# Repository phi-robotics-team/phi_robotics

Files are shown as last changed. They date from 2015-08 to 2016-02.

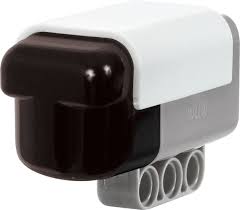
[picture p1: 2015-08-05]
notebook/alpha/2014-15 Phi Alpha Engineering Notebook/index.jpg

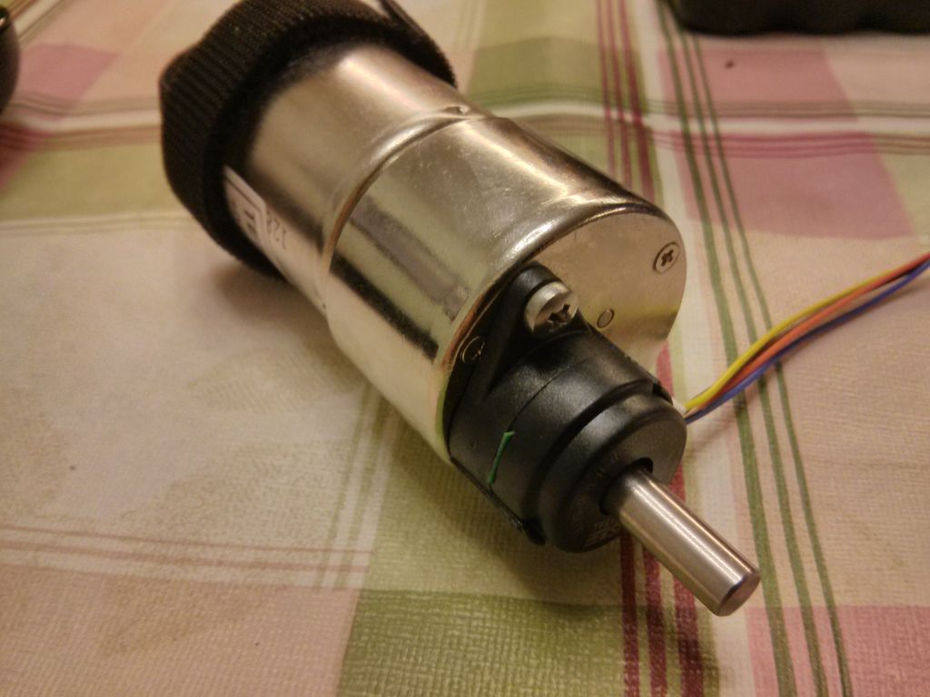
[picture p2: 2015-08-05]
notebook/alpha/2014-15 Phi Alpha Engineering Notebook/F77ZLUBHK46G527.LARGE.jpg

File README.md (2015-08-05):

# PHI Robotics

This repository is for the PHI teams to store all of their files into (replacement for BitSync).
All information should be stored here for easy access by both teams.

## Branch information

### Docs
Contains added once/not changed documents such as PDFs, styleguides, templates, etc

### Pictures
Pictures are in the Google drive area, not in Github

### Code
Contains two sub-directories, one for Alpha and one for Omega

### Notebook
Contains two sub-directories, one for Alpha and one for Omega

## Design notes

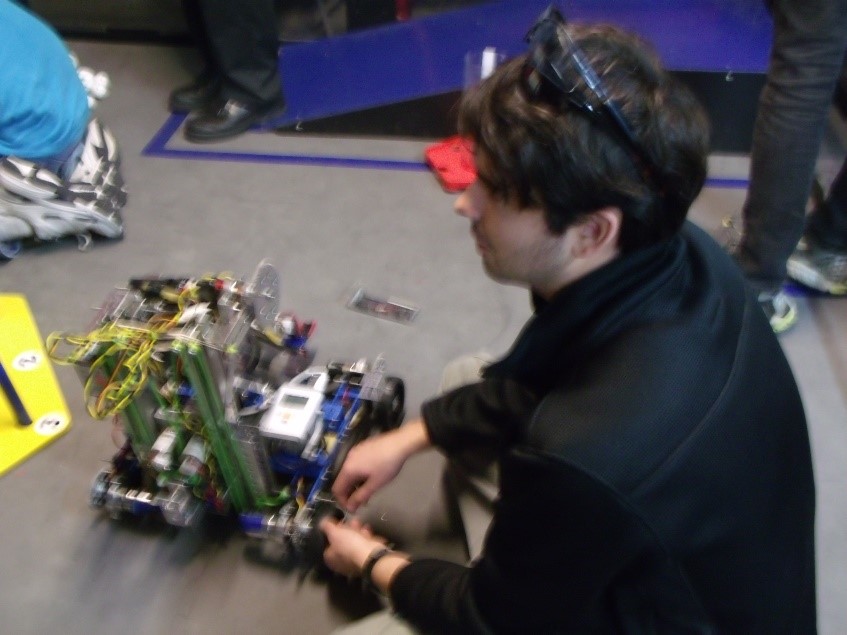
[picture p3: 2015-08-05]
notebook/omega/PHI Notebook 2014-2015/robot 1.jpg

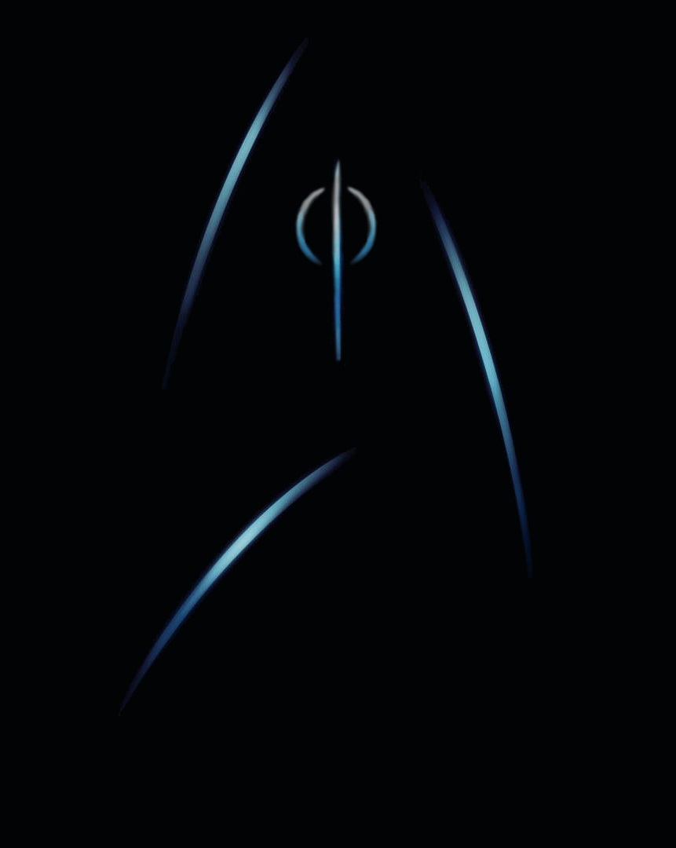
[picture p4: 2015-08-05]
notebook/omega/PHI Notebook 2014-2015/phitrek.jpg

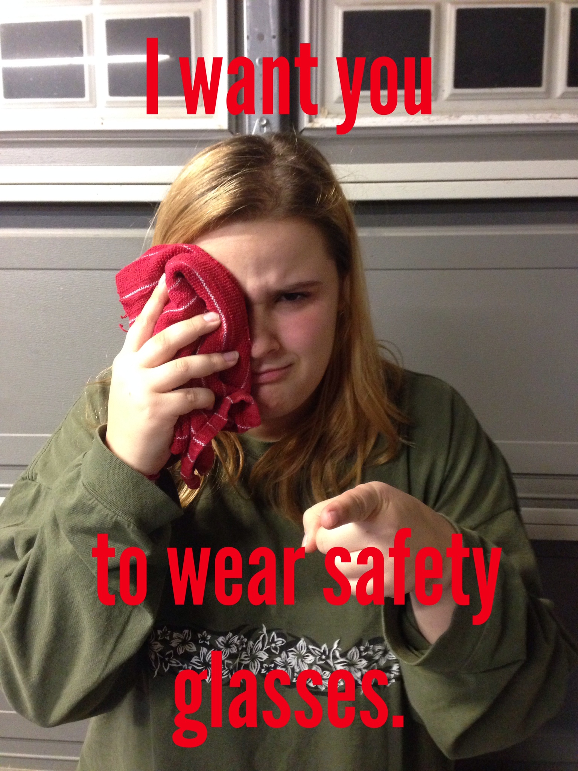
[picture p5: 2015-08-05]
misc/Plankt0n5 2014.11.03_0.JPG

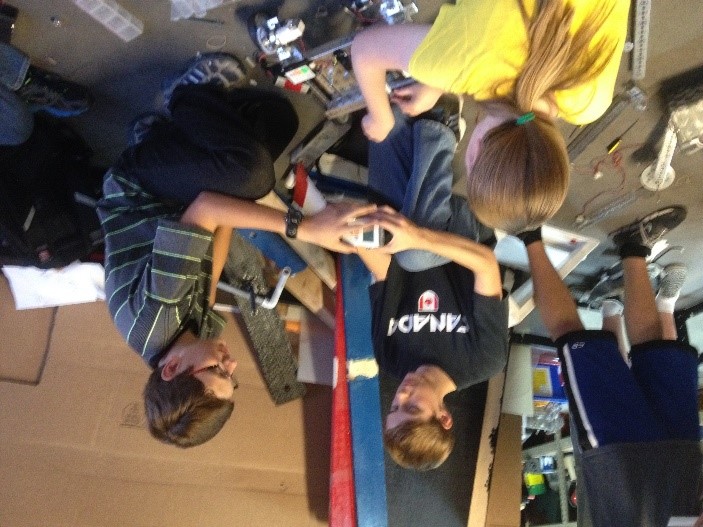
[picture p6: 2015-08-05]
notebook/omega/PHI Notebook 2014-2015/meeting.jpg

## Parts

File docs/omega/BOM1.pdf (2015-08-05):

Part name | Quantity | Game manual rule
PVC Pipe | Two and one-half feet | <RO4a>
Spray paint | Fourteen fluid ounces | <R12>
Lexan plastic | Three square feet | <RO4a>
Craft foam | Nine square inches | <RO4a>
Zip ties | Fifty zip ties | <RO5>
Surgical rubber tubing | Four feet | <RG10>
1/16 inch metal wire | Seven feet | <R10d>
Wire sheathing | Seven inches | <R10d>
Duct tape | Forty inches | <RO5>
Sheet metal | Twenty-one square inches | <RO4a>
Light Bars | Two | <R12>
Liquid accent highlighet ink | A 1/16 pen's worth | <R12>
Stickers | Thirteen | <R12>
Vectran | One-hundred inches | <RO4a>
Light Strip | One | <R12>
Carbon Fiber | Three square feet | <R12>
Printer Paper | Eight square inches | <R12>
Extended Power Wires | Three feet | <R10d>
Safety wire | Nine inches | <RO5>
Bungie | Six inches | <RG10>
Heat shrink | Seven inches | <R10d>
Threadlock | Two drops | <RO5>
Elmer's glue | Two fluid ounces | <R12>
Heavy duty silicone lube | One-quarter fluid ounce | <RO6>
Non-slip drawer liner | One-hundred square inches | <RO4a>
Phone cables | Seventy-five inches | <R10d>
ABS plastic | Thirty-two square inches | <RO4a>
Rivets | Twenty-one | <R12>
.40 cal shell casings | Seven | <RO4b>
Washers | Twenty-seven | <RO5>
Fender washers | One | <RO5>
Screen door roller | One | <RO4c>
Solder | Two inches | <RO5>
WD40 | One-sixteenth fluid once | <RO6>
Super glue | Three ounces | <RO5>
24 guage wire | Twelve inches | <R10d>
Velcro | Three inches | <RO5>
Nine-volt battery | One | <R11di>
Thread | Four feet | <RO4b>
Prototype board | One | <R11d>
Resister | Three | <RO8d>
GY-80 | One | <RO8d>
Light sensor | One | <RO8d>
Bowled over led strip | One | <R11e>
Surge protector usb | One | <RO8c>
Power polles | Four | <R10c>
Anderson connectors | Two | <R10c>
Axicom D2N relay | One | <RO8d>
Arduino NANO | One | <R11dii>
Solder board | One | <RO8Dd>
MUX | One | <R11b>
Ferrite choke | Two | <RO8c>
Poliester netting | One foot square | <RO4b>
Drawer slides | Three | <RO4c>
BILL OF MATERIALS | 4322

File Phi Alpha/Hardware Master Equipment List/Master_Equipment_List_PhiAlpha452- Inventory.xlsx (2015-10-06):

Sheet: Inventory List
INVENTORY LIST |  |  |  |  |  |  |  |  | Inventory
 | part Number | Part Name | Description | size | Color | Vendor | Price | units/pack | Quantity | Total
Channels
 | AZ39069 | TETRIX_739069_2012 | 416mm Channel |  |  | Pitsco(tetrix) | $17.95 | 1 | 0 | $0.00
 | AZ39068 | TETRIX_739068_2012 | 288mm Channel |  |  | Pitsco(tetrix) | $27.95 | 2 | 0 | $0.00
 | AZ39067 | TETRIX_739067_2012 | 160m Channel |  |  | Pitsco(tetrix) | $16.95 | 2 | 0 | $0.00
 | AZ39066 | TETRIX_739066_2012 | 96mm Channel |  |  | Pitsco(tetrix) | $11.95 | 2 | 0 | $0.00
 | AZ39065 | TETRIX_739065_2012 | 32mm Channel |  |  | Pitsco(tetrix) | $9.95 | 2 | 0 | $0.00
 |  |  |  |  |  |  |  |  | 0
Brackets |  |  |  |  |  |  |  |  | 0
 | AZ39061 | TETRIX_739061_2012 | Flat Bracket |  |  | Pitsco(tetrix) | $5.95 | 2 | 0 | $0.00
 | AZ39062 | TETRIX_739062_2012 | L Bracket |  |  | Pitsco(tetrix) | $4.95 | 2 | 0 | $0.00
 | AZ39281 |  | Inside Corner Bracket |  |  | Pitsco(Tetrix) | $4.95 | 2 | 0 | $0.00
 | AZ39270 | TETRIX_739270_2013 | Inside C Connector |  |  | Pitsco(tetrix) | $4.95 | 2 | 0 | $0.00
 |  |  |  |  |  |  |  |  | 0
Angles |  |  |  |  |  |  |  |  | 0
 | AZ39071 | TETRIX_739071_2012 | 288mm Angle |  |  | Pitsco(tetrix) | $13.95 | 2 | 0 | $0.00
 | AZ39072 | TETRIX_739072_2012 | 144mm Angle |  |  | Pitsco(tetrix) | $10.95 | 2 | 0 | $0.00
 |  |  |  |  |  |  |  |  | 0
Plates |  |  |  |  |  |  |  |  | 0
 | AZ39073 | TETRIX_739073_2012 | Flat Building Plate |  |  | Pitsco(tetrix) | $12.95 | 2 | 0 | $0.00
 |  |  |  |  |  |  |  |  | 0
Axles/Shafts |  |  |  |  |  |  |  |  | 0
 | AZ39088 |  | Axle | 100mm |  | Pitsco(tetrix) | $15.95 | 6 | 0 | $0.00
 | AZ35871 |  | Axle | 250mm |  | Pitsco(tetrix) | $15.95 | 3 | 0 | $0.00
 | AZ39172 |  | Axle Hub | Axle |  | Pitsco(tetrix) | $6.95 | 2 | 0 | $0.00
 | W39172 | TETRIX_739172_ 2012 | Axel Hub |  |  | Pitsco(tetrix) | $6.95 | 2 | 0 | $0.00
 | AZ39092 | TETRIX_739092_ 2012 | Axel Collar |  |  | Pitsco(tetrix) | $3.95 | 6 | 0 | $0.00
 | W39100 | TETRIX_739100_2012 | 1/8" Axel Spacer |  |  | Pitsco(tetrix) | $1.95 | 12 | 0 | $0.00
 | W39101 | TETRIX_739101_2012 | 3/8" Axel Spacer |  |  | Pitsco(tetrix) | $0.95 | 6 | 0 | $0.00
 |  |  |  |  |  |  |  |  | 0
Chains/Sprockets |  |  |  |  |  |  |  |  | 0
 | AZ39173 |  | Chain with Links |  |  | Pitsco(tetrix) | $13.95 | 5 feet | 0 | $0.00
 | AZ39171 | Tetrix Max 32-Tooth Sprocket Pack | Chain sprockets | 32 |  | Pitsco(tetrix) | $29.95 | 2 | 0 | $0.00
 | Az39169 | Tetrix Max 24-Tooth Sprocket Pack | Chain sprockets | 24 |  | Pitsco(tetrix) | $22.95 | 2 | 0 | $0.00
 | Az39165 | Tetrix Max 16-Tooth Sprocket Pack | Chain sprockets | 16 |  | Pitsco(tetrix) | $16.95 | 2 | 0 | $0.00
 |  |  |  |  |  |  |  |  | 0
Gears |  |  |  |  |  |  |  |  | 0
 | AZ39085 | TETRIX_731901_120_2013 | 120-Tooth Gear |  |  | Pitsco(tetrix) | $27.95 | 2 | 0 | $0.00
 | AZ39086 | TETRIX_739086_2012 | 80-Tooth Gear |  |  | Pitsco(tetrix) | $17.95 | 1 | 0 | $0.00
 | AZ39028 | TETRIX_739028_2012 | 40-Tooth Gear |  |  | Pitsco(tetrix) | $22.95 | 2 | 0 | $0.00
 | AZ39090 | TETRIX_739090_2012 | Gear Hub Spacer |  |  | Pitsco(tetrix) | $6.95 | 2 | 0 | $0.00
 | AZ38007 | Tetrix Max Vevel Gear & Acetal Bearings |  |  |  | Pitsco(tetrix) | $29.95 | 1 | 0 | $0.00
 | AZ39375 | Tetrix Max Worm Gear Box | 4:1 worm gear |  |  | Pitsco(tetrix) | $34.95 | 1 | 0 | $0.00
 |  |  |  |  |  |  |  |  | 0
Motors |  |  |  |  |  |  |  |  | 0
 | AM-3103 | NEVEREST_60_MOTOR | Motor with encoder | 1.46"dia |  | Andymark | $25.00 | 1 | 0 | $0.00
 | AZ39530 | TETRIX_739083_2012 | TETRIX DC Motor |  |  | Pitsco(tetrix) | $24.95 | 1 | 0 | $0.00 | 6 DC motors | Order from andy aMark with encoder.
 | AZ39079 | TETRIX_739079_2012 | Motor Hub |  |  | Pitsco(tetrix) | $5.95 | 2 | 0 | $0.00
 | AZ39089 |  | Motor Mount |  |  | Pitsco(tetrix) | $15.95 | 1 | 0 | $0.00
 | AZ39376 | TETRIX_739089_2012 | DC Motor Mount |  |  | Pitsco(tetrix) | $15.95 | 1 | 0 | $0.00 |  | Verify
 | W3989 | TETRIX_MAXMOTORMOUNT | MOTOR MOUNT |  |  | Pitsco(tetrix) | $15.95 | 1 | 0 | $0.00
 |  | TETRIX_739172_ 2012 | Motor Mount Screw |  |  | Pitsco(tetrix) |  |  | 0 | $0.00
 | AZ31903 |  | Motor power cable |  |  | Pitsco(tetrix) | $1.95 | 1 | 0 | $0.00
 | AZ36465 | TETRIX_731903_2012 | Motor Power Wire |  |  | Pitsco(tetrix) | $1.95 | 1 | 0 | $0.00
 | AM-2992 | hall_affect_encoder_cable | encoder cable with 4_pin connector | 19.5" |  | AndyMark | $5.00 | 1 | 0 | $0.00
 | w380000 | TETRIX_738000_2012 | Motor Encoder |  |  | Pitsco(tetrix) | $79.95 | 1 | 0 | $0.00
 |  |  |  |  |  |  |  |  | 0
Servo's |  |  |  |  |  |  |  |  | 0
 | AZ39197 |  | 180 servo |  |  | Pitsco(tetrix) | $24.95 | 1 | 0 | $0.00
 | AZ39060 | TETRIX_739060_2012 | Single Standard Scale Servo Bracket |  |  | Pitsco(tetrix) | $9.95 | 2 | 0 | $0.00
 | AZ39197 | TETRIX_739172_ 2012 | Standard-Scale HS-485HB Servo Motor |  |  | Pitsco(tetrix) | $24.95 | 1 | 0 | $0.00
 |  |  |  |  |  |  |  |  | 0
Controllers / Power distribution |  |  |  |  |  |  |  |  | 0
 | AZ34303 | Core_motor Controller |  |  |  | Pitsco(tetrix) | $89.95 | 1 | 0 | $0.00 |  | have 3- don't know how many work.
 |  | Core_Power_Distribution_Module |  |  |  |  |  |  | 0 | $0.00 |  | Have 1 new one
 | AZ34302 | Core_Servo_Controller |  |  |  | Pitsco(tetrix) | $79.95 | 1 | 0 | $0.00
 |  |  |  |  |  |  |  |  | 0
Wires |  |  |  |  |  |  |  |  | 0
 |  | Power (14 gauge (black white)
 | 7088k211 | Retracting Cable (300V AC-Light Duty) | 18 Gauge 2 wire | 2ft, 18ga |  | (McMaster-Carr) | $25.52 | 1 | 0 | $0.00
 |  |  |  |  |  |  |  |  | 0
Wheels |  |  |  |  |  |  |  |  | 0
 | AZ39055 | TETRIX_739055_2012 | 4" Wheel | 4" |  | Pitsco(tetrix) | $19.95 | 1 | 0 |  |  | Check with Andy Mark
 | AZ36466 | TETRIX_736466_2012 | TETRIX MAX Omni Wheel Pack | 4 inch |  | Pitsco(tetrix) | $29.95 | 2 | 0 | $0.00
 | W36466 |  | TETRIX MAX Omni Wheel Pack | 4" |  | Pitsco(tetrix) | $29.95 | 2 | 0 | $0.00
 |  |  |  |  |  |  |  |  | 0
Screws/Nuts |  |  |  |  |  |  |  |  | 0
 | AZ39098 |  | Small screw | Small |  | pitsco(Tetrix) | $9.95 | 100 | 0 | $0.00
 | AZ39097 |  | Medium screw | Medium |  | Pitsco(tetrix) | $9.95 | 100 | 0 | $0.00
 | AZ39111 |  | Flat screws | 3 8 |  | Pitsco(tetrix) | $8.95 | 50 | 0 | $0.00
 | AZ39094 | TETRIX_739094_2013 | Kep Nut |  |  | Pitsco(tetrix) | $2.95 | 100 | 0 | $0.00
 | W39097 | TETRIX_739097_2013 | 1/2" Socket Head Cap Screw |  |  | Pitsco(tetrix) | $9.95 | 100 | 0 | $0.00
 | W39098 | TETRIX_739098_2012 | 5/16" Socket Head Cap Screw |  |  | Pitsco(tetrix) | $9.95 | 100 | 0 | $0.00
 | W39111 | TETRIX_739111_2012 | Button Head Cap Screw |  |  | Pitsco(tetrix) | $8.95 | 50 | 0 | $0.00
 |  |  |  |  |  |  |  |  | 0
 |  |  |  |  |  |  |  |  | 0
Batteries |  |  |  |  |  |  |  |  | 0
 | AZ39057 | TETRIX_739057_2012 | Battery Pack | 12 Volt - NIMH |  | Pitsco(tetrix) | $49.95 | 1 | 0 | $0.00
 | AZ38009 | TETRIX_738009_BATPACK_BRKT_2013 | Battery Clip |  |  | Pitsco(tetrix) | $5.95 | 1 | 0 | $0.00
 | az39830 | TETRIX | Battery Pack Charger |  |  | Pitsco(tetrix) | $24.95 | 1 | 0 | $0.00
 |  |  |  |  |  |  |  |  | 0
Tools |  |  |  |  |  |  |  |  | 0
 | AZ39217 |  | Chain Breaker Tool |  |  | Pitsco(tetrix) | $16.95 |  | 0 | $0.00
 | W39104 |  | Hex Keys | 7/64, 3/32, 1/16, 5/64 |  | Pitsco(tetrix) | $0.95 | 4 each size | 0 | $0.00
 |  |  |  |  |  |  |  |  | 0
Miscellaneous Small Parts |  |  |  |  |  |  |  |  | 0
 | 8800k43 |  | Kevlar Thread | 346 |  | McMaster carr | $27.17 | 66 yards | 0 | $0.00
 | 87635k63 |  | polyester thread | 693 |  | McMaster carr | $12.77 | 120 yards | 0 | $0.00
 | 3434T33 |  | thread pulleys | 3 64 |  | MCMaster carr | $1.52 | 1 | 0 | $0.00
 |  |  |  |  |  |  |  |  | 0
 |  |  |  |  |  |  |  |  | 0
 | W39102 | TETRIX_739102_2012 | 1" Stand-off |  |  | Pitsco(tetrix) | $3.95 | 12 | 0 | $0.00
 | W39107 | TETRIX_739107_2013 | 32mm Stand-of |  |  | Pitsco(tetrix) | $4.95 | 12 | 0 | $0.00
 | AZ39091 | TETRIX_739091_2013 | Bronze Bushing |  |  | Pitsco(tetrix) | $13.95 | 12 | 0 | $0.00
 | W39120 | TETRIX_739120_2012 | Hard Point Connector |  |  | Pitsco(tetrix) | $12.00 | 12 | 0 | $0.00
 |  |  |  |  |  |  |  |  |  | $0.00

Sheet: order (4)
 | part Number | Part Name | Description | size | Color | Vendor | Price | units/pack | Quantity | Total
 | 7088k211 | Retracting Cable (300V AC-Light Duty) | 18 Gauge 2 wire | 2ft, 18ga |  | McMaster-Carr | $25.52 | 1 | 1 | $25.52
 | AM-2992 | hall_affect_encoder_cable | encoder cable with 4_pin connector | 19.5" |  | Andy Mark | $5.00 | 1 | 8 | $40.00
 | AM-2964 | Nev Rest 40 Motor | 40:1 Motor |  |  | Andy Mark | $25.00 | 1 | 4 | $100.00
 | am-3211 | Bonded Wire | 18 Gauge 2 wire 20'' | 20'', 18 |  | Andy Mark | $7.00 | 25 | 1 | $7.00
 | AM-0980 | Polycarbonate sheet | 24"x24", 0.118" | 0.118" |  | Andy Mark | $20.00 | 1 | 2 | $40.00
 |  | Gyro |  |  |  | HiTechnic
 | 9697T2 | Easy-ID Low-Voltage Cable | 18 Gauge 2 wire black/red | 50ft, 18 ga |  | McMaster carr | $15.50 | 1 | 0 | $0.00 |  | McCloud may be getting wire
 | 73095K48 | Heat-Shrink Tubing Assortments |  |  |  | McMaster carr | $27.12 | 1 | 0 | $0.00
 | 45-2018 | Color Sensor |  |  |  | Modern Robotics, Inc | $36.95 | 1 | 0 | $0.00 |  | Order if we can program the Hi technic sensor.
 | AZ39062 | TETRIX_739062_2012 | L Bracket |  |  | Pitsco(tetrix) | $4.95 | 2 | 0 | $0.00
 | AUA3030 | Core Device Interface Module |  |  |  | Modern Robotics, Inc. | $67.95 | 1 | 0 | $0.00 |  | Order if we go with the color sensor.
 | GPF0310 | Logitec F310 Gamepad |  |  |  | Modern Robotics, Inc. | $24.95 | 1 | 1 | $24.95
 | W36468 | Tetrix Max Tank Tread Kit |  |  |  | Pitsco (Tetrix) | $99.95 | 1 | 1 | $99.95
 | W36464 | Tetrix Max Tank Tread Inserts |  |  |  | Pitsco (Tetrix) | $17.95 | 1 | 1 | $17.95
 | W39069/AZ39069 | TETRIX_739069_2012 | 416mm Channel | 16.4 |  | Pitsco(tetrix) | $17.95 | 1 | 0 | $0.00
 | W39068/AZ39068 | TETRIX_739068_2012 | 288mm Channel | 11.3 |  | Pitsco(tetrix) | $27.95 | 2 | 1 | $27.95
 | W39067/AZ39067 | TETRIX_739067_2012 | 160m Channel | 6.3 |  | Pitsco(tetrix) | $16.95 | 2 | 1 | $16.95
 | W39066/AZ39066 | TETRIX_739066_2012 | 96mm Channel | 3.8 |  | Pitsco(tetrix) | $11.95 | 2 | 3 | $35.85
 | W39065/AZ39065 | TETRIX_739065_2012 | 32mm Channel | 1.3 |  | Pitsco(tetrix) | $9.95 | 2 | 2 | $19.90
 | W39061/AZ39061 | TETRIX_739061_2012 | Flat Bracket |  |  | Pitsco(tetrix) | $5.95 | 2 | 4 | $23.80
 | W39281/AZ39281 |  | Inside Corner Bracket |  |  | Pitsco(Tetrix) | $4.95 | 2 | 3 | $14.85
 | W39270/AZ39270 | TETRIX_739270_2013 | Inside C Connector |  |  | Pitsco(tetrix) | $4.95 | 2 | 4 | $19.80
 | W39071/AZ39071 | TETRIX_739071_2012 | 288mm Angle |  |  | Pitsco(tetrix) | $13.95 | 2 | 2 | $27.90
 | AZ39172 |  | Axle Hub | Axle |  | Pitsco(tetrix) | $6.95 | 2 | 0 | $0.00
 | W39072/AZ39072 | TETRIX_739072_2012 | 144mm Angle |  |  | Pitsco(tetrix) | $10.95 | 2 | 2 | $21.90
 | W39073/AZ39073 | TETRIX_739073_2012 | Flat Building Plate |  |  | Pitsco(tetrix) | $12.95 | 2 | 1 | $12.95
 | W39100 | TETRIX_739100_2012 | 1/8" Axel Spacer |  |  | Pitsco(tetrix) | $1.95 | 12 | 0 | $0.00
 | W39101 | TETRIX_739101_2012 | 3/8" Axel Spacer |  |  | Pitsco(tetrix) | $0.95 | 6 | 0 | $0.00
 | W39088/AZ39088 |  | Axle | 100mm |  | Pitsco(tetrix) | $15.95 | 6 | 1 | $15.95
 | W35871/AZ35871 |  | Axle | 250mm |  | Pitsco(tetrix) | $15.95 | 3 | 1 | $15.95
 | W39173/AZ39173 |  | Chain with Links |  |  | Pitsco(tetrix) | $13.95 | 5 feet | 0 | $0.00
 | W39171/AZ39171 | Tetrix Max 32-Tooth Sprocket Pack | Chain sprockets | 32.0 |  | Pitsco(tetrix) | $29.95 | 2 | 0 | $0.00
 | W39169/Az39169 | Tetrix Max 24-Tooth Sprocket Pack | Chain sprockets | 24.0 |  | Pitsco(tetrix) | $22.95 | 2 | 0 | $0.00
 | W39165/Az39165 | Tetrix Max 16-Tooth Sprocket Pack | Chain sprockets | 16.0 |  | Pitsco(tetrix) | $16.95 | 2 | 0 | $0.00
 | W39172 | TETRIX_739172_ 2012 | Axel Hub |  |  | Pitsco(tetrix) | $6.95 | 2 | 4 | $27.80
 | W39092/AZ39092 | TETRIX_739092_ 2012 | Axel Collar |  |  | Pitsco(tetrix) | $3.95 | 6 | 2 | $7.90
 | W39085/AZ39085 | TETRIX_731901_120_2013 | 120-Tooth Gear |  |  | Pitsco(tetrix) | $27.95 | 2 | 1 | $27.95
 | AZ39086 | TETRIX_739086_2012 | 80-Tooth Gear |  |  | Pitsco(tetrix) | $17.95 | 1 | 0 | $0.00
 | AZ39028 | TETRIX_739028_2012 | 40-Tooth Gear |  |  | Pitsco(tetrix) | $22.95 | 2 | 0 | $0.00
 | W39090/AZ39090 | TETRIX_739090_2012 | Gear Hub Spacer |  |  | Pitsco(tetrix) | $6.95 | 2 | 4 | $27.80
 | AZ38007 | Tetrix Max Vevel Gear & Acetal Bearings |  |  |  | Pitsco(tetrix) | $29.95 | 1 | 0 | $0.00
 | AZ39375 | Tetrix Max Worm Gear Box | 4:1 worm gear |  |  | Pitsco(tetrix) | $34.95 | 1 | 0 | $0.00
 | AZ39060 | TETRIX_739060_2012 | Single Standard Scale Servo Bracket |  |  | Pitsco(tetrix) | $9.95 | 2 | 1 | $9.95
 | AZ34303 | Core_motor Controller |  |  |  | Pitsco(tetrix) | $89.95 | 1 | 0 | $0.00 |  | have 3- don't know how many work.
 | AM-3103 | NEVEREST_60_MOTOR | Motor with encoder | 1.46"dia |  | Andymark | $25.00 | 1 | 0 | $0.00
 | AZ39530 | TETRIX_739083_2012 | TETRIX DC Motor |  |  | Pitsco(tetrix) | $24.95 | 1 | 0 | $0.00 | 6 DC motors | Order from andy aMark with encoder.
 | AZ39079 | TETRIX_739079_2012 | Motor Hub |  |  | Pitsco(tetrix) | $5.95 | 2 | 0 | $0.00
 | AZ39089 |  | Motor Mount |  |  | Pitsco(tetrix) | $15.95 | 1 | 0 | $0.00
 | AZ39376 | TETRIX_739089_2012 | DC Motor Mount |  |  | Pitsco(tetrix) | $15.95 | 1 | 0 | $0.00 |  | Verify
 | W3989 | TETRIX_MAXMOTORMOUNT | MOTOR MOUNT |  |  | Pitsco(tetrix) | $15.95 | 1 | 0 | $0.00
 |  | TETRIX_739172_ 2012 | Motor Mount Screw |  |  | Pitsco(tetrix) |  |  | 0 | $0.00
 | W31903/AZ31903 |  | Motor power cable |  |  | Pitsco(tetrix) | $1.95 | 1 | 0 | $0.00
 | AZ36465 | TETRIX_731903_2012 | Motor Power Wire |  |  | Pitsco(tetrix) | $1.95 | 1 | 0 | $0.00
 | AZ34302 | Core_Servo_Controller |  |  |  | Pitsco(tetrix) | $79.95 | 1 | 0 | $0.00
 | w380000 | TETRIX_738000_2012 | Motor Encoder |  |  | Pitsco(tetrix) | $79.95 | 1 | 0 | $0.00
 | W39104 |  | Hex Keys | 7/64, 3/32, 1/16, 5/64 |  | Pitsco(tetrix) | $0.95 | 4 each size | 2 | $1.90
 | W39102 | TETRIX_739102_2012 | 1" Stand-off |  |  | Pitsco(tetrix) | $3.95 | 12 | 1 | $3.95
 | AZ39197 |  | 180 servo |  |  | Pitsco(tetrix) | $24.95 | 1 | 0 | $0.00
 | W39107 | TETRIX_739107_2013 | 32mm Stand-of |  |  | Pitsco(tetrix) | $4.95 | 12 | 1 | $4.95
 | AZ39197 | TETRIX_739172_ 2012 | Standard-Scale HS-485HB Servo Motor |  |  | Pitsco(tetrix) | $24.95 | 1 | 0 | $0.00
Channels
Brackets
Angles
Plates
Axles/Shafts
Chains/Sprockets
Gears
 |  | Power (14 gauge (black white)
Motors
Servo's
Controllers / Power distribution
 | W39055/AZ39055 | TETRIX_739055_2012 | 4" Wheel | 4" |  | Pitsco(tetrix) | $19.95 | 1 | 0 | $0.00 |  | Check with Andy Mark
 | AZ36466 | TETRIX_736466_2012 | TETRIX MAX Omni Wheel Pack | 4 inch |  | Pitsco(tetrix) | $29.95 | 2 | 0 | $0.00
 | W36466 |  | TETRIX MAX Omni Wheel Pack | 4" |  | Pitsco(tetrix) | $29.95 | 2 | 0 | $0.00
 |  | Core_Power_Distribution_Module |  |  |  |  |  |  | 0 | $0.00 |  | Have 1 new one
Sensors
Wires
Wheels
Tread Kits
 | 94985K911 | Super Adhesive-back General Purpose Hook and Loop | 2" x 5 ft |  |  | McMaster-Carr | $17.91 | 1 | 0 | $0.00
Polycarbonate Sheet
 | AZ39098 |  | Small screw | Small |  | pitsco(Tetrix) | $9.95 | 100 | 0 | $0.00
 | AZ39097 |  | Medium screw | Medium |  | Pitsco(tetrix) | $9.95 | 100 | 0 | $0.00
 | AZ39111 |  | Flat screws | 3 8 |  | Pitsco(tetrix) | $8.95 | 50 | 0 | $0.00
 | AZ39094 | TETRIX_739094_2013 | Kep Nut |  |  | Pitsco(tetrix) | $2.95 | 100 | 0 | $0.00
 | W39097 | TETRIX_739097_2013 | 1/2" Socket Head Cap Screw |  |  | Pitsco(tetrix) | $9.95 | 100 | 0 | $0.00
 | W39098 | TETRIX_739098_2012 | 5/16" Socket Head Cap Screw |  |  | Pitsco(tetrix) | $9.95 | 100 | 0 | $0.00
 | W39111 | TETRIX_739111_2012 | Button Head Cap Screw |  |  | Pitsco(tetrix) | $8.95 | 50 | 0 | $0.00
Velcro
Screws/Nuts
 | AZ39057 | TETRIX_739057_2012 | Battery Pack | 12 Volt - NIMH |  | Pitsco(tetrix) | $49.95 | 1 | 0 | $0.00
 | AZ38009 | TETRIX_738009_BATPACK_BRKT_2013 | Battery Clip |  |  | Pitsco(tetrix) | $5.95 | 1 | 0 | $0.00
 | az39830 | TETRIX | Battery Pack Charger |  |  | Pitsco(tetrix) | $24.95 | 1 | 0 | $0.00
 | AZ39217 |  | Chain Breaker Tool |  |  | Pitsco(tetrix) | $16.95 |  | 0 | $0.00
Batteries
Tools
 | 8800k43 |  | Kevlar Thread | 346.0 |  | McMaster carr | $27.17 | 66 yards | 0 | $0.00
 | 87635k63 |  | polyester thread | 693.0 |  | McMaster carr | $12.77 | 120 yards | 0 | $0.00
 | 3434T33 |  | thread pulleys | 3 64 |  | MCMaster carr | $1.52 | 1 | 0 | $0.00
Miscellaneous Small Parts
 | AZ39091 | TETRIX_739091_2013 | Bronze Bushing |  |  | Pitsco(tetrix) | $13.95 | 12 | 0 | $0.00
 | W39120 | TETRIX_739120_2012 | Hard Point Connector |  |  | Pitsco(tetrix) | $12.00 | 12 | 0 | $0.00
 |  |  |  |  |  |  |  |  |  | $721.32
 |  | Tread & Inserts
 |  | Color Sensor
 |  | 18 gauge wire
 |  | Polycarbonate
 |  | Color Sensor | Check with Caddics
 |  | Velcro

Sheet: Sheet1
part Number | Part Name | Description | size | Color | Vendor | Price | units/pack | Quantity | Total
AZ39069 |  | C-channel | 416mm |  | Pitsco(Tetrix) | $17.95 | 1 | 4 | $71.80 | 16.64 | 416 | 16.64
AZ39281 |  | Inside Corner Bracket |  |  | Pitsco(Tetrix) | $4.95 | 2 | 4 | $19.80 |  | 288 | 11.52
AZ39098 |  | Small screw | Small |  | pitsco(Tetrix) | $9.95 | 100 | 1 | $9.95
AZ39097 |  | Medium screw | Medium |  | Pitsco(tetrix) | $9.95 | 100 | 1 | $9.95
AZ39094 |  | Kep Nuts |  |  | Pitsco(tetrix) | $2.95 | 100 | 2 | $5.90
AZ39111 |  | Flat screws | 3 8 |  | Pitsco(tetrix) | $8.95 | 50 | 1 | $8.95
AZ39197 |  | 180 servo |  |  | Pitsco(tetrix) | $24.95 | 1 | 4 | $99.80
AZ39172 |  | Axle Hub | Axle |  | Pitsco(tetrix) | $6.95 | 2 | 4 | $27.80
AZ39088 |  | Axle | 100mm |  | Pitsco(tetrix) | $15.95 | 6 | 1 | $15.95
AZ35871 |  | Axle | 250mm |  | Pitsco(tetrix) | $15.95 | 3 | 2 | $31.90
AZ39079 |  | Motor Shaft Hubs | Motor |  | Pitsco(tetrix) | $5.95 | 2 | 2 | $11.90
AZ39173 |  | Chain with Links |  |  | Pitsco(tetrix) | $13.95 | 5 feet | 1 | $13.95
AZ39057 |  | 12volt nimh battery pack | 12 volt |  | Pitsco(tetrix) | $49.95 | 1 | 2 | $99.90
AZ39104 |  | Hex Keys | Each size |  | Pitsco(tetrix) | $0.95 | 4 each size | 15 | $14.25
AZ39217 |  | Chain Breaker Tool |  |  | Pitsco(tetrix) | $16.95 | 1 | 1 | $16.95
 |  | motor controller |  |  | Pitsco(tetrix) |  |  |  | $0.00
 |  | servo controller |  |  | Pitsco(tetrix) |  |  |  | $0.00
AZ39055 |  | Wheel | 4” |  | Pitsco(tetrix) | $19.95 | 1 | 4 | $79.80
AZ39089 |  | Motor Mount |  |  | Pitsco(tetrix) | $15.95 | 1 | 6 | $95.70
AZ31903 |  | Motor power cable |  |  | Pitsco(tetrix) | $1.95 | 1 | 5 | $9.75
8800k43 |  | Kevlar Thread | 346 |  | McMaster carr | $27.17 | 66 yards | 1 | $27.17
87635k63 |  | polyester thread | 693 |  | McMaster carr | $12.77 | 120 yards | 1 | $12.77
3434T33 |  | tread pulleys | 3 64 |  | MCMaster carr | $1.52 | 1 | 4 | $6.08
AZ34303 | Core_motor Controller |  |  |  | Pitsco(tetrix) | $89.95 | 1
 | Core_Power_Distribution_Module
AZ34302 | Core_Servo_Controller |  |  |  | Pitsco(tetrix) | $79.95 | 1
AZ39085 | TETRIX_731901_120_2013 | 120-Tooth Gear |  |  | Pitsco(tetrix) | $27.95 | 2
AZ36465 | TETRIX_731903_2012 | Motor Power Wire |  |  | Pitsco(tetrix) | $1.95 | 1
AZ36466 | TETRIX_736466_2012 | 4” Dual Omni Wheel Assembly |  |  | Pitsco(tetrix) | $29.95 | 2
w380000 | TETRIX_738000_2012 | Motor Encoder |  |  | Pitsco(tetrix) | $79.95 | 1 | 0
AZ38009 | TETRIX_738009_BATPACK_BRKT_2013 | Battery Clip |  |  | Pitsco(tetrix) | $5.95 | 1
AZ39028 | TETRIX_739028_2012 | 40-Tooth Gear |  |  | Pitsco(tetrix) | $22.95 | 2
AZ39055 | TETRIX_739055_2012 | 4" Wheel |  |  | Pitsco(tetrix) | $19.95 | 1
AZ39057 | TETRIX_739057_2012 | Battery Pack |  |  | Pitsco(tetrix) | $49.95 | 1
az39830 | TETRIX | Battery Pack Charger |  |  | Pitsco(tetrix) | $24.95 | 1
AZ39060 | TETRIX_739060_2012 | Single Standard Scale Servo Bracket |  |  | Pitsco(tetrix) | $9.95 | 2
AZ39061 | TETRIX_739061_2012 | Flat Bracket |  |  | Pitsco(tetrix) | $5.95 | 2
AZ39062 | TETRIX_739062_2012 | L Bracket |  |  | Pitsco(tetrix) | $4.95 | 2
AZ39065 | TETRIX_739065_2012 | 32mm Channel |  |  | Pitsco(tetrix) | $9.95 | 2
AZ39066 | TETRIX_739066_2012 | 96mm Channel |  |  | Pitsco(tetrix) | $11.95 | 2
AZ39067 | TETRIX_739067_2012 | 160m Channel |  |  | Pitsco(tetrix) | $16.95 | 2
AZ39068 | TETRIX_739068_2012 | 288mm Channel |  |  | Pitsco(tetrix) | $27.95 | 2
AZ39069 | TETRIX_739069_2012 | 416mm Channel |  |  | Pitsco(tetrix) | $17.95 | 1
AZ39071 | TETRIX_739071_2012 | 288mm Angle |  |  | Pitsco(tetrix) | $13.95 | 2
AZ39072 | TETRIX_739072_2012 | 144mm Angle |  |  | Pitsco(tetrix) | $10.95 | 2
AZ39073 | TETRIX_739073_2012 | Flat Building Plage |  |  | Pitsco(tetrix) | $12.95 | 2
AZ39079 | TETRIX_739079_2012 | Motor Hub |  |  | Pitsco(tetrix) | $5.95 | 2
AZ39530 | TETRIX_739083_2012 | TETRIX DC Motor |  |  | Pitsco(tetrix) | $24.95 | 1
AZ39086 | TETRIX_739086_2012 | 80-Tooth Gear |  |  | Pitsco(tetrix) | $17.95 | 1
AZ39088 | TETRIX_739088_2013 | 100 mm Axle |  |  | Pitsco(tetrix) | $15.95 | 6
AZ35871 | TETRIX | 250 mm Axle |  |  | Pitsco(tetrix) | $15.95 | 3
AZ39376 | TETRIX_739089_2012 | DC Motor Mount |  |  | Pitsco(tetrix) | $15.95 | 1
AZ39090 | TETRIX_739090_2012 | Gear Hub Spacer |  |  | Pitsco(tetrix) | $6.95 | 2
AZ39091 | TETRIX_739091_2013 | Bronze Bushing |  |  | Pitsco(tetrix) | $13.95 | 12
AZ39092 | TETRIX_739092_ 2012 | Axel Collar |  |  | Pitsco(tetrix) | $3.95 | 6
AZ39094 | TETRIX_739094_2013 | Kep Nut |  |  | Pitsco(tetrix) | $2.95 | 100
W39097 | TETRIX_739097_2013 | 1/2" Socket Head Cap Screw |  |  | Pitsco(tetrix) | $9.95 | 100 | 1
W39098 | TETRIX_739098_2012 | 5/16" Socket Head Cap Screw |  |  | Pitsco(tetrix) | $9.95 | 100 | 1
W39100 | TETRIX_739100_2012 | 1/8" Axel Spacer |  |  | Pitsco(tetrix) | $1.95 | 12 | 1
W39101 | TETRIX_739101_2012 | 3/8" Axel Spacer |  |  | Pitsco(tetrix) | $0.95 | 6
W39102 | TETRIX_739102_2012 | 1" Stand-off |  |  | Pitsco(tetrix) | $3.95 | 12
W39107 | TETRIX_739107_2013 | 32mm Stand-of |  |  | Pitsco(tetrix) | $4.95 | 12
W39111 | TETRIX_739111_2012 | Button Head Cap Screw |  |  | Pitsco(tetrix) | $8.95 | 50
W39120 | TETRIX_739120_2012 | Hard Point Connector |  |  | Pitsco(tetrix) | $12.00 | 12
W39172 | TETRIX_739172_ 2012 | Axel Hub |  |  | Pitsco(tetrix) | $6.95 | 2
 | TETRIX_739172_ 2012 | Motor Mount Screw |  |  | Pitsco(tetrix)
AZ39197 | TETRIX_739172_ 2012 | Standard-Scale HS-485HB Servo Motor |  |  | Pitsco(tetrix) | $24.95 | 1
AZ39270 | TETRIX_739270_2013 | Inside C Connector |  |  | Pitsco(tetrix) | $4.95 | 2
AZ39090 | TETRIX | Gear Hub Spacers |  |  | Pitsco(tetrix) | $6.95 | 2
W3989 | TETRIX_MAXMOTORMOUNT | MOTOR MOUNT |  |  | Pitsco(tetrix) | $15.95 | 1
AM-3103 | NEVEREST_60_MOTOR | Motor with encoder | 1.46"dia |  | Andymark | $25.00 | 1
AM-2992 | hall_affect_encoder_cable | encoder cable with 4_pin connector | 19.5" |  | AndyMark | $5.00 | 1

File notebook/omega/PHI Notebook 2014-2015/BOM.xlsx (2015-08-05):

BILL OF MATERIALS
Part name | Quantity | Game manual reference
Abs plastic | 32 square inches
Non-slip drawer liner | 100 square inches
Spray paint | 60 fluid ounces
Lexan plastic | 3 square feet
Craft foam | 9 square inches
Zip ties | 50 zip-ties
Surgical rubber tubing | 4 feet
String | 100 inches
Wire sheathing | 7 inches
Duct tape | 40 inches
Sheet metal | 21 square inches
Rivets | 21 rivets
Phone Cables | 75 inches
PVC Pipe | 2 1/2 feet

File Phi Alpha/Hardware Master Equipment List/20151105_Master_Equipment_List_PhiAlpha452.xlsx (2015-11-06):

 | part Number | Part Name | Description | size | Color | Vendor | Price | units/pack | Quantity | Total
Channels
 | AZ39069 | TETRIX_739069_2012 | 416mm Channel |  |  | Pitsco(tetrix) | $17.95 | 1 | 0 | $0.00
 | AZ39068 | TETRIX_739068_2012 | 288mm Channel |  |  | Pitsco(tetrix) | $27.95 | 2 | 0 | $0.00
 | AZ39067 | TETRIX_739067_2012 | 160m Channel |  |  | Pitsco(tetrix) | $16.95 | 2 | 0 | $0.00
 | AZ39066 | TETRIX_739066_2012 | 96mm Channel |  |  | Pitsco(tetrix) | $11.95 | 2 | 0 | $0.00
 | AZ39065 | TETRIX_739065_2012 | 32mm Channel |  |  | Pitsco(tetrix) | $9.95 | 2 | 0 | $0.00
Brackets
 | AZ39061 | TETRIX_739061_2012 | Flat Bracket |  |  | Pitsco(tetrix) | $5.95 | 2 | 0 | $0.00
 | AZ39062 | TETRIX_739062_2012 | L Bracket |  |  | Pitsco(tetrix) | $4.95 | 2 | 0 | $0.00
 | AZ39281 |  | Inside Corner Bracket |  |  | Pitsco(Tetrix) | $4.95 | 2 | 0 | $0.00
 | AZ39270 | TETRIX_739270_2013 | Inside C Connector |  |  | Pitsco(tetrix) | $4.95 | 2 | 0 | $0.00
Angles
 | AZ39071 | TETRIX_739071_2012 | 288mm Angle |  |  | Pitsco(tetrix) | $13.95 | 2 | 0 | $0.00
 | AZ39072 | TETRIX_739072_2012 | 144mm Angle |  |  | Pitsco(tetrix) | $10.95 | 2 | 0 | $0.00
Plates
 | AZ39073 | TETRIX_739073_2012 | Flat Building Plate |  |  | Pitsco(tetrix) | $12.95 | 2 | 1 | $12.95
Axles/Shafts
 | AZ39088 |  | Axle | 100mm |  | Pitsco(tetrix) | $15.95 | 6 | 0 | $0.00
 | AZ35871 |  | Axle | 250mm |  | Pitsco(tetrix) | $15.95 | 3 | 1 | $15.95
 | AZ39172 |  | Axle Hub | Axle |  | Pitsco(tetrix) | $6.95 | 2 | 0 | $0.00
 | W39172 | TETRIX_739172_ 2012 | Axel Hub |  |  | Pitsco(tetrix) | $6.95 | 2 | 4 | $27.80
 | AZ39092 | TETRIX_739092_ 2012 | Axel Collar |  |  | Pitsco(tetrix) | $3.95 | 6 | 2 | $7.90
 | W39100 | TETRIX_739100_2012 | 1/8" Axel Spacer |  |  | Pitsco(tetrix) | $1.95 | 12 | 2 | $3.90
 | W39101 | TETRIX_739101_2012 | 3/8" Axel Spacer |  |  | Pitsco(tetrix) | $0.95 | 6 | 0 | $0.00
Chains/Sprockets
 | W39174 | Tetrix Max Sprocket and Chain Pack |  |  |  | Pitsco(tetrix) | $69.96 | 1 | 1 | $69.96
 | AZ39173 |  | Chain with Links |  |  | Pitsco(tetrix) | $13.95 | 5 feet | 0 | $0.00
 | AZ39171 | Tetrix Max 32-Tooth Sprocket Pack | Chain sprockets | 32 |  | Pitsco(tetrix) | $29.95 | 2 | 0 | $0.00
 | Az39169 | Tetrix Max 24-Tooth Sprocket Pack | Chain sprockets | 24 |  | Pitsco(tetrix) | $22.95 | 2 | 0 | $0.00
 | Az39165 | Tetrix Max 16-Tooth Sprocket Pack | Chain sprockets | 16 |  | Pitsco(tetrix) | $16.95 | 2 | 0 | $0.00
Gears
 | AZ39085 | TETRIX_731901_120_2013 | 120-Tooth Gear |  |  | Pitsco(tetrix) | $27.95 | 1 | 4 | $111.80
 | AZ39086 | TETRIX_739086_2012 | 80-Tooth Gear |  |  | Pitsco(tetrix) | $17.95 | 1 | 0 | $0.00
 | AZ39028 | TETRIX_739028_2012 | 40-Tooth Gear |  |  | Pitsco(tetrix) | $22.95 | 2 | 0 | $0.00
 | W39090 | TETRIX_739090_2012 | Gear Hub Spacer |  |  | Pitsco(tetrix) | $6.95 | 2 | 3 | $20.85
 | AZ38007 | Tetrix Max Vevel Gear & Acetal Bearings |  |  |  | Pitsco(tetrix) | $29.95 | 1 | 0 | $0.00
 | AZ39375 | Tetrix Max Worm Gear Box | 4:1 worm gear |  |  | Pitsco(tetrix) | $34.95 | 1 | 0 | $0.00
Motors
 | AM-3103 | NEVEREST_60_MOTOR | Motor with encoder | 1.46"dia |  | Andymark | $25.00 | 1 | 0 | $0.00
 | AZ39530 | TETRIX_739083_2012 | TETRIX DC Motor |  |  | Pitsco(tetrix) | $24.95 | 1 | 0 | $0.00 | 6 DC motors | Order from andy aMark with encoder.
 | AZ39079 | TETRIX_739079_2012 | Motor Hub |  |  | Pitsco(tetrix) | $5.95 | 2 | 0 | $0.00
 | AZ39089 |  | Motor Mount |  |  | Pitsco(tetrix) | $15.95 | 1 | 0 | $0.00
 | AZ39376 | TETRIX_739089_2012 | DC Motor Mount |  |  | Pitsco(tetrix) | $15.95 | 1 | 0 | $0.00 |  | Verify
 | W3989 | TETRIX_MAXMOTORMOUNT | MOTOR MOUNT |  |  | Pitsco(tetrix) | $15.95 | 1 | 0 | $0.00
 |  | TETRIX_739172_ 2012 | Motor Mount Screw |  |  | Pitsco(tetrix) |  |  | 0 | $0.00
 | AZ31903 |  | Motor power cable |  |  | Pitsco(tetrix) | $1.95 | 1 | 0 | $0.00
 | AZ36465 | TETRIX_731903_2012 | Motor Power Wire |  |  | Pitsco(tetrix) | $1.95 | 1 | 0 | $0.00
 | AM-2992 | hall_affect_encoder_cable | encoder cable with 4_pin connector | 19.5" |  | AndyMark | $5.00 | 1 | 0 | $0.00
 | w380000 | TETRIX_738000_2012 | Motor Encoder |  |  | Pitsco(tetrix) | $79.95 | 1 | 0 | $0.00
Servo's
 | AZ39197 |  | 180 servo |  |  | Pitsco(tetrix) | $24.95 | 1 | 0 | $0.00
 | W39060 | TETRIX_739060_2012 | Single Standard Scale Servo Bracket |  |  | Pitsco(tetrix) | $9.95 | 2 | 1 | $9.95
 | AZ39197 | TETRIX_739172_ 2012 | Standard-Scale HS-485HB Servo Motor |  |  | Pitsco(tetrix) | $24.95 | 1 | 0 | $0.00
 | W39280 | Tetrix Max Adjustable Servo Brackets |  |  |  | Pitsco(tetrix) | $10.95 | 1 | 1 | $10.95
Controllers / Power distribution
 | AZ34303 | Core_motor Controller |  |  |  | Pitsco(tetrix) | $89.95 | 1 | 0 | $0.00 |  | have 3- don't know how many work.
 |  | Core_Power_Distribution_Module |  |  |  |  |  |  | 0 | $0.00 |  | Have 1 new one
 | AZ34302 | Core_Servo_Controller |  |  |  | Pitsco(tetrix) | $79.95 | 1 | 0 | $0.00
Cables
 | SKU:45-1122 | OTG USB Cable | Power distribution to Android phone |  |  | Modern Robotics | $6.95 | 1 | 2 | $13.90
 | SKU: 50-1003 | USB Mini Cable Kit | Core Modules to the USB Hub |  |  | Modern Robotics | $8.95 | 2 | 0 | $0.00 |  | out of Stock
 |  | Cable Matters: Micro-USB 2.0 On-The-Go Adapter 6 inch |  |  |  | Amazon | $6.99 | 2 | 1 | $6.99
Wires
 |  | Power (14 gauge (black white)
 | 7088k211 | Retracting Cable (300V AC-Light Duty) | 18 Gauge 2 wire | 2ft, 18ga |  | (McMaster-Carr) | $25.52 | 1 | 0 | $0.00 |  | Look into smaller gauge - look for terminal strips - check ftc Rules
Wheels
 | AZ39055 | TETRIX_739055_2012 | 4" Wheel | 4" |  | Pitsco(tetrix) | $19.95 | 1 | 0 | $0.00 |  | Check with Andy Mark
 | AZ36466 | TETRIX_736466_2012 | TETRIX MAX Omni Wheel Pack | 4 inch |  | Pitsco(tetrix) | $29.95 | 2 | 0 | $0.00
 | W36466 |  | TETRIX MAX Omni Wheel Pack | 4" |  | Pitsco(tetrix) | $29.95 | 2 | 0 | $0.00
Treads
 | W36468 |  | Tetrix Max Tank Tread Kit |  |  | Pitsco (Tetrix) | $99.95 | 1 | 0 | $0.00 |  | Re-think this - Treads have'nt been working -get spare track - skp paddles - do we want to use an Idler for a spool?
 | W39250 |  | Tetrix Max Tank Tread Accessory Pack |  |  | Pitsco (Tetrix) | $32.95 | 1 | 0 | $0.00
Screws/Nuts
 | AZ39098 |  | Small screw | Small |  | pitsco(Tetrix) | $9.95 | 100 | 0 | $0.00
 | AZ39097 |  | Medium screw | Medium |  | Pitsco(tetrix) | $9.95 | 100 | 0 | $0.00
 | AZ39111 |  | Flat screws | 3 8 |  | Pitsco(tetrix) | $8.95 | 50 | 0 | $0.00
 | AZ39094 | TETRIX_739094_2013 | Kep Nut |  |  | Pitsco(tetrix) | $2.95 | 100 | 0 | $0.00
 | W39097 | TETRIX_739097_2013 | 1/2" Socket Head Cap Screw |  |  | Pitsco(tetrix) | $9.95 | 100 | 0 | $0.00
 | W39098 | TETRIX_739098_2012 | 5/16" Socket Head Cap Screw |  |  | Pitsco(tetrix) | $9.95 | 100 | 0 | $0.00
 | W39111 | TETRIX_739111_2012 | Button Head Cap Screw |  |  | Pitsco(tetrix) | $8.95 | 50 | 0 | $0.00
Batteries
 | W39057 | TETRIX_739057_2012 | Battery Pack | 12 Volt - NIMH |  | Pitsco(tetrix) | $49.95 | 1 | 1 | $49.95
 | AZ38009 | TETRIX_738009_BATPACK_BRKT_2013 | Battery Clip |  |  | Pitsco(tetrix) | $5.95 | 1 | 0 | $0.00
 | az39830 | TETRIX | Battery Pack Charger |  |  | Pitsco(tetrix) | $24.95 | 1 | 0 | $0.00
 | W39129 | Tetrix | On/Off Switch |  |  | Pitsco(tetrix) | $6.95 | 1 | 0 | $0.00 |  | Do we need this?
 | W39176 | Tetrix | Switch Mounting Bracket |  |  | Pitsco(tetrix) | $2.95 | 1 | 0 | $0.00
Sensors
 | SKU: 45-2018 | Color Sensor |  |  |  | Modern Robotics | $36.95 | 1 | 0 | $0.00 |  | Out of Stock
 | SKU: 45-2005 | Integrating Gyro |  |  |  | Modern Robotics | $32.96 | 1 | 0 | $0.00 |  | Learn to use existing gyro first
Tools
 | AZ39217 |  | Chain Breaker Tool |  |  | Pitsco(tetrix) | $16.95 |  | 0 | $0.00
 | W39104 |  | Hex Keys | 7/64, 3/32, 1/16, 5/64 |  | Pitsco(tetrix) | $0.95 | 4 each size | 2 | $1.90
Miscellaneous Small Parts
 | 8800k43 |  | Kevlar Thread | 346 |  | McMaster carr | $27.17 | 66 yards | 1 | $27.17
 | 87635k63 |  | polyester thread | 693 |  | McMaster carr | $12.77 | 120 yards | 0 | $0.00
 | 3434T33 |  | thread pulleys | 3 64 |  | MCMaster carr | $1.52 | 1 | 12 | $18.24 |  | Re veryify size - get matching screws and nuts for mounting
 | W39102 | TETRIX_739102_2012 | 1" Stand-off |  |  | Pitsco(tetrix) | $3.95 | 12 | 0 | $0.00
 | W39107 | TETRIX_739107_2013 | 32mm Stand-of |  |  | Pitsco(tetrix) | $4.95 | 12 | 0 | $0.00
 | AZ39091 | TETRIX_739091_2013 | Bronze Bushing |  |  | Pitsco(tetrix) | $13.95 | 12 | 0 | $0.00
 | W39120 | TETRIX_739120_2012 | Hard Point Connector |  |  | Pitsco(tetrix) | $12.00 | 12 | 0 | $0.00
 |  |  |  |  |  |  |  |  |  | $0.00
 | SKU: 50-1104 | Phone Mount Kit | mounts phone to robot |  |  | Modern Robotics | $6.96 | 1 | 1 | $6.96
 |  |  | USB-USB mini Connector
 |  |  |  |  |  |  |  |  |  | $417.12

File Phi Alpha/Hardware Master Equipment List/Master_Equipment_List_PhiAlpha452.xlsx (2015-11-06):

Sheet: order (4)
 | part Number | Part Name | Description | size | Color | Vendor | Price | units/pack | Quantity | Total
 | 7088k211 | Retracting Cable (300V AC-Light Duty) | 18 Gauge 2 wire | 2ft, 18ga |  | McMaster-Carr | $25.52 | 1 | 1 | $25.52
 | AM-2992 | hall_affect_encoder_cable | encoder cable with 4_pin connector | 19.5" |  | Andy Mark | $5.00 | 1 | 8 | $40.00
 | AM-2964 | Nev Rest 40 Motor | 40:1 Motor |  |  | Andy Mark | $25.00 | 1 | 4 | $100.00
 | am-3211 | Bonded Wire | 18 Gauge 2 wire 20'' | 20'', 18 |  | Andy Mark | $7.00 | 25 | 1 | $7.00
 | AM-0980 | Polycarbonate sheet | 24"x24", 0.118" | 0.118" |  | Andy Mark | $20.00 | 1 | 2 | $40.00
 |  | Gyro |  |  |  | HiTechnic
 | 9697T2 | Easy-ID Low-Voltage Cable | 18 Gauge 2 wire black/red | 50ft, 18 ga |  | McMaster carr | $15.50 | 1 | 0 | $0.00 | McCloud may be getting wire
 | 73095K48 | Heat-Shrink Tubing Assortments |  |  |  | McMaster carr | $27.12 | 1 | 0 | $0.00
 | 45-2018 | Color Sensor |  |  |  | Modern Robotics, Inc | $36.95 | 1 | 0 | $0.00 | Order if we can program the Hi technic sensor.
 | AUA3030 | Core Device Interface Module |  |  |  | Modern Robotics, Inc. | $67.95 | 1 | 0 | $0.00 | Order if we go with the color sensor.
 | GPF0310 | Logitec F310 Gamepad |  |  |  | Modern Robotics, Inc. | $24.95 | 1 | 1 | $24.95
 | W36468 | Tetrix Max Tank Tread Kit |  |  |  | Pitsco (Tetrix) | $99.95 | 1 | 1 | $99.95
 | W36464 | Tetrix Max Tank Tread Inserts |  |  |  | Pitsco (Tetrix) | $17.95 | 1 | 1 | $17.95
 | W39069/AZ39069 | TETRIX_739069_2012 | 416mm Channel | 16.4 |  | Pitsco(tetrix) | $17.95 | 1 | 0 | $0.00
 | W39068/AZ39068 | TETRIX_739068_2012 | 288mm Channel | 11.3 |  | Pitsco(tetrix) | $27.95 | 2 | 1 | $27.95
 | W39067/AZ39067 | TETRIX_739067_2012 | 160m Channel | 6.3 |  | Pitsco(tetrix) | $16.95 | 2 | 1 | $16.95
 | W39066/AZ39066 | TETRIX_739066_2012 | 96mm Channel | 3.8 |  | Pitsco(tetrix) | $11.95 | 2 | 3 | $35.85
 | W39065/AZ39065 | TETRIX_739065_2012 | 32mm Channel | 1.3 |  | Pitsco(tetrix) | $9.95 | 2 | 2 | $19.90
 | W39061/AZ39061 | TETRIX_739061_2012 | Flat Bracket |  |  | Pitsco(tetrix) | $5.95 | 2 | 4 | $23.80
 | W39281/AZ39281 |  | Inside Corner Bracket |  |  | Pitsco(Tetrix) | $4.95 | 2 | 3 | $14.85
 | W39270/AZ39270 | TETRIX_739270_2013 | Inside C Connector |  |  | Pitsco(tetrix) | $4.95 | 2 | 4 | $19.80
 | W39071/AZ39071 | TETRIX_739071_2012 | 288mm Angle |  |  | Pitsco(tetrix) | $13.95 | 2 | 2 | $27.90
 | W39072/AZ39072 | TETRIX_739072_2012 | 144mm Angle |  |  | Pitsco(tetrix) | $10.95 | 2 | 2 | $21.90
 | W39073/AZ39073 | TETRIX_739073_2012 | Flat Building Plate |  |  | Pitsco(tetrix) | $12.95 | 2 | 1 | $12.95
 | W39088/AZ39088 |  | Axle | 100mm |  | Pitsco(tetrix) | $15.95 | 6 | 1 | $15.95
 | W35871/AZ35871 |  | Axle | 250mm |  | Pitsco(tetrix) | $15.95 | 3 | 1 | $15.95
 | W39172 | TETRIX_739172_ 2012 | Axel Hub |  |  | Pitsco(tetrix) | $6.95 | 2 | 4 | $27.80
 | W39092/AZ39092 | TETRIX_739092_ 2012 | Axel Collar |  |  | Pitsco(tetrix) | $3.95 | 6 | 2 | $7.90
 | W39085/AZ39085 | TETRIX_731901_120_2013 | 120-Tooth Gear |  |  | Pitsco(tetrix) | $27.95 | 2 | 1 | $27.95
 | W39090/AZ39090 | TETRIX_739090_2012 | Gear Hub Spacer |  |  | Pitsco(tetrix) | $6.95 | 2 | 4 | $27.80
 | AZ39060 | TETRIX_739060_2012 | Single Standard Scale Servo Bracket |  |  | Pitsco(tetrix) | $9.95 | 2 | 1 | $9.95
 | AZ34303 | Core_motor Controller |  |  |  | Pitsco(tetrix) | $89.95 | 1 | 0 | $0.00 | have 3- don't know how many work.
 | AZ34302 | Core_Servo_Controller |  |  |  | Pitsco(tetrix) | $79.95 | 1 | 0 | $0.00
Channels
Brackets
Angles
Plates
Axles/Shafts
Chains/Sprockets
Gears
Motors
Servo's
Controllers / Power distribution
 | W39055/AZ39055 | TETRIX_739055_2012 | 4" Wheel | 4" |  | Pitsco(tetrix) | $19.95 | 1 | 0 | $0.00 | Check with Andy Mark
 | AZ36466 | TETRIX_736466_2012 | TETRIX MAX Omni Wheel Pack | 4 inch |  | Pitsco(tetrix) | $29.95 | 2 | 0 | $0.00
 | W36466 |  | TETRIX MAX Omni Wheel Pack | 4" |  | Pitsco(tetrix) | $29.95 | 2 | 0 | $0.00
 |  | Core_Power_Distribution_Module |  |  |  |  |  |  | 0 | $0.00 | Have 1 new one
Sensors
Wires
Wheels
Tread Kits
Polycarbonate Sheet
Velcro
Screws/Nuts
Batteries
Tools
 | W39104 |  | Hex Keys | 7/64, 3/32, 1/16, 5/64 |  | Pitsco(tetrix) | $0.95 | 4 each size | 2 | $1.90
Miscellaneous Small Parts
 | W39102 | TETRIX_739102_2012 | 1" Stand-off |  |  | Pitsco(tetrix) | $3.95 | 12 | 1 | $3.95
 | AZ39197 |  | 180 servo |  |  | Pitsco(tetrix) | $24.95 | 1 | 0 | $0.00
 | W39107 | TETRIX_739107_2013 | 32mm Stand-of |  |  | Pitsco(tetrix) | $4.95 | 12 | 1 | $4.95
 |  | Tread & Inserts
 |  | Color Sensor
 |  | 18 gauge wire
 |  | Polycarbonate
 |  | Color Sensor | Check with Caddics
 |  | Velcro

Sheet: order (3)
 | part Number | Part Name | Description | size | Color | Vendor | Price | units/pack | Quantity | Total
Channels
 | AZ39069 | TETRIX_739069_2012 | 416mm Channel |  |  | Pitsco(tetrix) | $17.95 | 1 | 2 | $35.90
 | AZ39068 | TETRIX_739068_2012 | 288mm Channel |  |  | Pitsco(tetrix) | $27.95 | 2 | 1 | $27.95
 | AZ39067 | TETRIX_739067_2012 | 160m Channel |  |  | Pitsco(tetrix) | $16.95 | 2 | 1 | $16.95
 | AZ39066 | TETRIX_739066_2012 | 96mm Channel |  |  | Pitsco(tetrix) | $11.95 | 2 | 3 | $35.85
 | AZ39065 | TETRIX_739065_2012 | 32mm Channel |  |  | Pitsco(tetrix) | $9.95 | 2 | 2 | $19.90
Brackets
 | AZ39061 | TETRIX_739061_2012 | Flat Bracket |  |  | Pitsco(tetrix) | $5.95 | 2 | 4 | $23.80
 | AZ39281 |  | Inside Corner Bracket |  |  | Pitsco(Tetrix) | $4.95 | 2 | 3 | $14.85
 | AZ39270 | TETRIX_739270_2013 | Inside C Connector |  |  | Pitsco(tetrix) | $4.95 | 2 | 4 | $19.80
Angles
 | AZ39071 | TETRIX_739071_2012 | 288mm Angle |  |  | Pitsco(tetrix) | $13.95 | 2 | 2 | $27.90
 | AZ39072 | TETRIX_739072_2012 | 144mm Angle |  |  | Pitsco(tetrix) | $10.95 | 2 | 2 | $21.90
Plates
 | AZ39073 | TETRIX_739073_2012 | Flat Building Plate |  |  | Pitsco(tetrix) | $12.95 | 2 | 1 | $12.95
Axles/Shafts
 | AZ39088 |  | Axle | 100mm |  | Pitsco(tetrix) | $15.95 | 6 | 1 | $15.95
 | AZ35871 |  | Axle | 250mm |  | Pitsco(tetrix) | $15.95 | 3 | 1 | $15.95
 | W39172 | TETRIX_739172_ 2012 | Axel Hub |  |  | Pitsco(tetrix) | $6.95 | 2 | 4 | $27.80
 | AZ39092 | TETRIX_739092_ 2012 | Axel Collar |  |  | Pitsco(tetrix) | $3.95 | 6 | 2 | $7.90
Chains/Sprockets
 | AZ39173 |  | Chain with Links |  |  | Pitsco(tetrix) | $13.95 | 5 feet | 1 | $13.95
 | AZ39171 | Tetrix Max 32-Tooth Sprocket Pack | Chain sprockets | 32 |  | Pitsco(tetrix) | $29.95 | 2 | 1 | $29.95
 | Az39169 | Tetrix Max 24-Tooth Sprocket Pack | Chain sprockets | 24 |  | Pitsco(tetrix) | $22.95 | 2 | 2 | $45.90
 | Az39165 | Tetrix Max 16-Tooth Sprocket Pack | Chain sprockets | 16 |  | Pitsco(tetrix) | $16.95 | 2 | 2 | $33.90
Gears
 | AZ39085 | TETRIX_731901_120_2013 | 120-Tooth Gear |  |  | Pitsco(tetrix) | $27.95 | 2 | 1 | $27.95
 | AZ39090 | TETRIX_739090_2012 | Gear Hub Spacer |  |  | Pitsco(tetrix) | $6.95 | 2 | 4 | $27.80
Motors
 | AZ31903 |  | Motor power cable |  |  | Pitsco(tetrix) | $1.95 | 1 | 2 | $3.90
 | AM-2992 | hall_affect_encoder_cable | encoder cable with 4_pin connector | 19.5" |  | AndyMark | $5.00 | 1 | 4 | $20.00
Servo's
 | AZ39060 | TETRIX_739060_2012 | Single Standard Scale Servo Bracket |  |  | Pitsco(tetrix) | $9.95 | 2 | 1 | $9.95
Controllers / Power distribution
Wires
 | 7088k211 | Retracting Cable (300V AC-Light Duty) | 18 Gauge 2 wire | 2ft, 18ga |  | (McMaster-Carr) | $25.52 | 1 | 1 | $25.52
Wheels
 | AZ39055 | TETRIX_739055_2012 | 4" Wheel | 4" |  | Pitsco(tetrix) | $19.95 | 1 | 2 | $39.90 | Check with Andy Mark
 | W36466 |  | TETRIX MAX Omni Wheel Pack | 4" |  | Pitsco(tetrix) | $29.95 | 2 | 1 | $29.95
Screws/Nuts
Batteries
Tools
 | AZ39217 |  | Chain Breaker Tool |  |  | Pitsco(tetrix) | $16.95 |  | 1 | $16.95
 | W39104 |  | Hex Keys | 7/64, 3/32, 1/16, 5/64 |  | Pitsco(tetrix) | $0.95 | 4 each size | 2 | $1.90
Miscellaneous Small Parts
 | W39102 | TETRIX_739102_2012 | 1" Stand-off |  |  | Pitsco(tetrix) | $3.95 | 12 | 1 | $3.95
 | W39107 | TETRIX_739107_2013 | 32mm Stand-of |  |  | Pitsco(tetrix) | $4.95 | 12 | 1 | $4.95
 |  |  |  |  |  |  |  |  |  | $661.77
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

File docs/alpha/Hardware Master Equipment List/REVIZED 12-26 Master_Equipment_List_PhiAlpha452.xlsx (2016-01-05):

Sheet: order (4)
 | part Number | Part Name | Description | size | Color | Vendor | Price | units/pack | Quantity | Total
Channels
 | W39069/AZ39069 | TETRIX_739069_2012 | 416mm Channel |  |  | Pitsco(tetrix) | $17.95 | 1 | 0 | $0.00
 | W39068/AZ39068 | TETRIX_739068_2012 | 288mm Channel |  |  | Pitsco(tetrix) | $27.95 | 2 | 0 | $0.00
 | W39067/AZ39067 | TETRIX_739067_2012 | 160m Channel |  |  | Pitsco(tetrix) | $16.95 | 2 | 0 | $0.00
 | W39066/AZ39066 | TETRIX_739066_2012 | 96mm Channel |  |  | Pitsco(tetrix) | $11.95 | 2 | 0 | $0.00
 | W39065/AZ39065 | TETRIX_739065_2012 | 32mm Channel |  |  | Pitsco(tetrix) | $9.95 | 2 | 0 | $0.00
Brackets
 | W39061/AZ39061 | TETRIX_739061_2012 | Flat Bracket |  |  | Pitsco(tetrix) | $5.95 | 2 | 3 | $17.85
 | AZ39062 | TETRIX_739062_2012 | L Bracket |  |  | Pitsco(tetrix) | $4.95 | 2 | 0 | $0.00
 | W39281/AZ39281 |  | Inside Corner Bracket |  |  | Pitsco(Tetrix) | $4.95 | 2 | 0 | $0.00
 | W39270/AZ39270 | TETRIX_739270_2013 | Inside C Connector |  |  | Pitsco(tetrix) | $4.95 | 2 | 3 | $14.85
Angles
 | W39071/AZ39071 | TETRIX_739071_2012 | 288mm Angle |  |  | Pitsco(tetrix) | $13.95 | 2 | 1 | $13.95
 | W39072/AZ39072 | TETRIX_739072_2012 | 144mm Angle |  |  | Pitsco(tetrix) | $10.95 | 2 | 1 | $10.95
Plates
 | W39073/AZ39073 | TETRIX_739073_2012 | Flat Building Plate |  |  | Pitsco(tetrix) | $12.95 | 2 | 0 | $0.00
Axles/Shafts
 | W39088/AZ39088 |  | Axle | 100mm |  | Pitsco(tetrix) | $15.95 | 6 | 1 | $15.95
 | W35871/AZ35871 |  | Axle | 250mm |  | Pitsco(tetrix) | $15.95 | 3 | 0 | $0.00
 | AZ39172 |  | Axle Hub | Axle |  | Pitsco(tetrix) | $6.95 | 2 | 0 | $0.00
 | W39172 | TETRIX_739172_ 2012 | Axel Hub |  |  | Pitsco(tetrix) | $6.95 | 2 | 2 | $13.90
 | W39092/AZ39092 | TETRIX_739092_ 2012 | Axel Collar |  |  | Pitsco(tetrix) | $3.95 | 6 | 2 | $7.90
 | W39100 | TETRIX_739100_2012 | 1/8" Axel Spacer |  |  | Pitsco(tetrix) | $1.95 | 12 | 0 | $0.00
 | W39101 | TETRIX_739101_2012 | 3/8" Axel Spacer |  |  | Pitsco(tetrix) | $0.95 | 6 | 0 | $0.00
Chains/Sprockets
 | W39173/AZ39173 |  | Chain with Links |  |  | Pitsco(tetrix) | $13.95 | 5 feet | 2 | $27.90
 | W39171/AZ39171 | Tetrix Max 32-Tooth Sprocket Pack | Chain sprockets | 32 |  | Pitsco(tetrix) | $29.95 | 2 | 1 | $29.95
 | W39169/Az39169 | Tetrix Max 24-Tooth Sprocket Pack | Chain sprockets | 24 |  | Pitsco(tetrix) | $22.95 | 2 | 2 | $45.90
 | W39165/Az39165 | Tetrix Max 16-Tooth Sprocket Pack | Chain sprockets | 16 |  | Pitsco(tetrix) | $16.95 | 2 | 4 | $67.80
Gears
 | W39085/AZ39085 | TETRIX_731901_120_2013 | 120-Tooth Gear |  |  | Pitsco(tetrix) | $27.95 | 2 | 0 | $0.00
 | AZ39086 | TETRIX_739086_2012 | 80-Tooth Gear |  |  | Pitsco(tetrix) | $17.95 | 1 | 0 | $0.00
 | AZ39028 | TETRIX_739028_2012 | 40-Tooth Gear |  |  | Pitsco(tetrix) | $22.95 | 2 | 0 | $0.00
 | W39090/AZ39090 | TETRIX_739090_2012 | Gear Hub Spacer |  |  | Pitsco(tetrix) | $6.95 | 2 | 0 | $0.00
 | AZ38007 | Tetrix Max Vevel Gear & Acetal Bearings |  |  |  | Pitsco(tetrix) | $29.95 | 1 | 0 | $0.00
 | AZ39375 | Tetrix Max Worm Gear Box | 4:1 worm gear |  |  | Pitsco(tetrix) | $34.95 | 1 | 0 | $0.00
Motors
 | AM-3103 | NEVEREST_60_MOTOR | Motor with encoder | 1.46"dia |  | Andymark | $25.00 | 1 | 0 | $0.00
 | AZ39530 | TETRIX_739083_2012 | TETRIX DC Motor |  |  | Pitsco(tetrix) | $24.95 | 1 | 0 | $0.00 | 6 DC motors | Order from andy aMark with encoder.
 | AZ39079 | TETRIX_739079_2012 | Motor Hub |  |  | Pitsco(tetrix) | $5.95 | 2 | 0 | $0.00
 | AZ39089 |  | Motor Mount |  |  | Pitsco(tetrix) | $15.95 | 1 | 0 | $0.00
 | AZ39376 | TETRIX_739089_2012 | DC Motor Mount |  |  | Pitsco(tetrix) | $15.95 | 1 | 0 | $0.00 |  | Verify
 | W3989 | TETRIX_MAXMOTORMOUNT | MOTOR MOUNT |  |  | Pitsco(tetrix) | $15.95 | 1 | 0 | $0.00
 |  | TETRIX_739172_ 2012 | Motor Mount Screw |  |  | Pitsco(tetrix) |  |  | 0 | $0.00
 | W31903/AZ31903 |  | Motor power cable |  |  | Pitsco(tetrix) | $1.95 | 1 | 0 | $0.00
 | AZ36465 | TETRIX_731903_2012 | Motor Power Wire |  |  | Pitsco(tetrix) | $1.95 | 1 | 0 | $0.00
 | AM-2992 | hall_affect_encoder_cable | encoder cable with 4_pin connector | 19.5" |  | AndyMark | $5.00 | 1 | 0 | $0.00
 | w380000 | TETRIX_738000_2012 | Motor Encoder |  |  | Pitsco(tetrix) | $79.95 | 1 | 0 | $0.00
Servo's
 | AZ39197 |  | 180 servo |  |  | Pitsco(tetrix) | $24.95 | 1 | 0 | $0.00
 | AZ39060 | TETRIX_739060_2012 | Single Standard Scale Servo Bracket |  |  | Pitsco(tetrix) | $9.95 | 2 | 0 | $0.00
 | AZ39197 | TETRIX_739172_ 2012 | Standard-Scale HS-485HB Servo Motor |  |  | Pitsco(tetrix) | $24.95 | 1 | 0 | $0.00
Controllers / Power distribution
 | AZ34303 | Core_motor Controller |  |  |  | Pitsco(tetrix) | $89.95 | 1 | 0 | $0.00 |  | have 3- don't know how many work.
 | AZ34302 | Core_Servo_Controller |  |  |  | Pitsco(tetrix) | $79.95 | 1 | 0 | $0.00
 |  | Core_Power_Distribution_Module |  |  |  |  |  |  | 0 | $0.00 |  | Have 1 new one
 | AUA3030 | Core Device Interface Module |  |  |  | Modern Robotics, Inc. | $67.95 | 1 | 0 | $0.00 |  | Order if we go with the color sensor.
 | GPF0310 | Logitec F310 Gamepad |  |  |  | Modern Robotics, Inc. | $24.95 | 1 | 0 | $0.00
Sensors
 | 45-2018 | Color Sensor |  |  |  | Modern Robotics, Inc | $36.95 | 1 | 0 | $0.00 |  | Order if we can program the Hi technic sensor.
Wires
 |  | Power (14 gauge (black white)
 | 7088k211 | Retracting Cable (300V AC-Light Duty) | 18 Gauge 2 wire | 2ft, 18ga |  | (McMaster-Carr) | $25.52 | 1 | 0 | $0.00
 | 9697T2 | Easy-ID Low-Voltage Cable | 18 Gauge 2 wire black/red | 50ft, 18 ga |  | McMaster carr | $15.50 | 1 | 0 | $0.00 |  | McCloud may be getting wire
 | 73095K48 | Heat-Shrink Tubing Assortments |  |  |  | McMaster carr | $27.12 | 1 | 0 | $0.00
Wheels
 | W39055/AZ39055 | TETRIX_739055_2012 | 4" Wheel | 4" |  | Pitsco(tetrix) | $19.95 | 1 | 0 | $0.00 |  | Check with Andy Mark
 | AZ36466 | TETRIX_736466_2012 | TETRIX MAX Omni Wheel Pack | 4 inch |  | Pitsco(tetrix) | $29.95 | 2 | 0 | $0.00
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

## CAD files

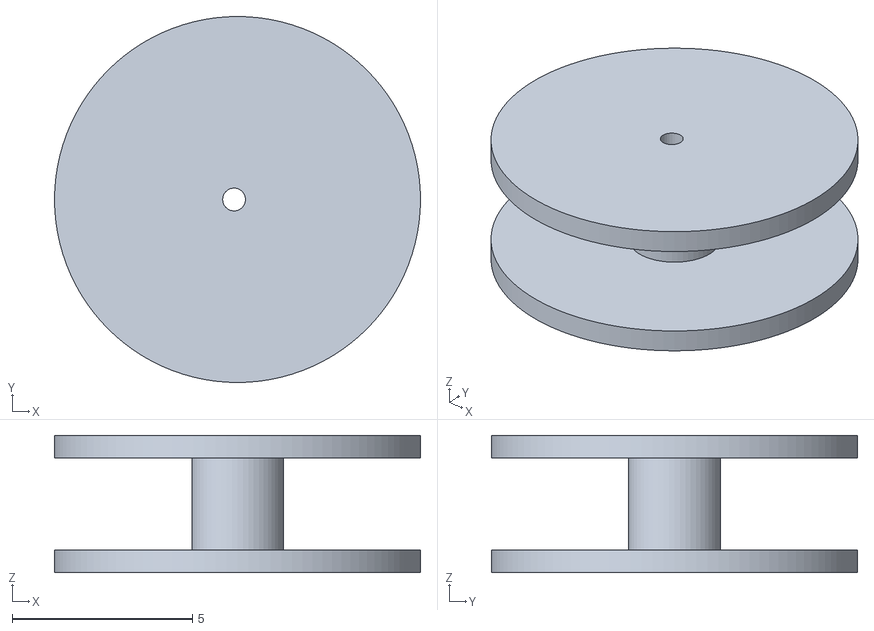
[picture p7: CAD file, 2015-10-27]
3d-models/FTC_Tetrix_KOP_Block_Party/spool model.stl
10.2 x 10.2 x 3.81

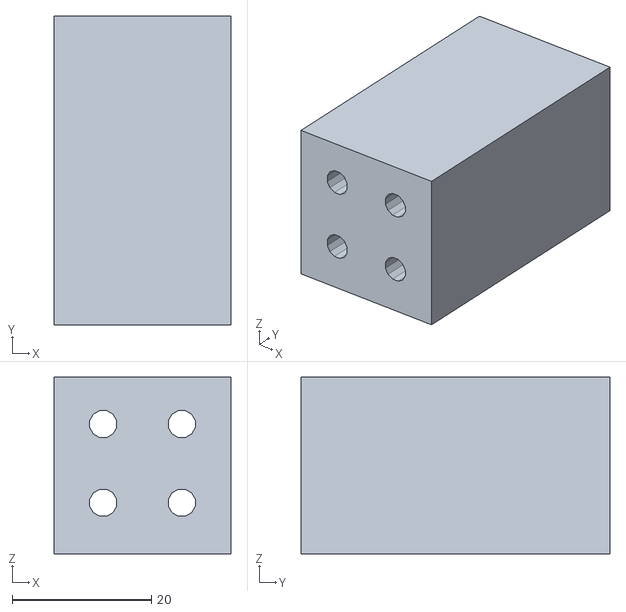
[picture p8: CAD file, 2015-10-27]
3d-models/omega/inventor/v-ger_bulkhead_block_2.stl
25.4 x 44.5 x 25.4

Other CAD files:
3d-models/FTC_Tetrix_KOP_Block_Party/Legacy Module.ipt
3d-models/FTC_Tetrix_KOP_Block_Party/Lego_Mindstorm_Kit_FTC/axle_10_2012.prt
3d-models/FTC_Tetrix_KOP_Block_Party/Lego_Mindstorm_Kit_FTC/axle_12_2012.prt
3d-models/FTC_Tetrix_KOP_Block_Party/Lego_Mindstorm_Kit_FTC/axle_3_2012.prt
3d-models/FTC_Tetrix_KOP_Block_Party/Lego_Mindstorm_Kit_FTC/axle_4_2012.prt
3d-models/FTC_Tetrix_KOP_Block_Party/Lego_Mindstorm_Kit_FTC/axle_5_2012.prt
3d-models/FTC_Tetrix_KOP_Block_Party/Lego_Mindstorm_Kit_FTC/axle_5half_2012.prt
3d-models/FTC_Tetrix_KOP_Block_Party/Lego_Mindstorm_Kit_FTC/axle_6_2012.prt
3d-models/FTC_Tetrix_KOP_Block_Party/Lego_Mindstorm_Kit_FTC/axle_8_2012.prt
3d-models/FTC_Tetrix_KOP_Block_Party/Lego_Mindstorm_Kit_FTC/axle_extender_2012.prt
3d-models/FTC_Tetrix_KOP_Block_Party/Lego_Mindstorm_Kit_FTC/axle_red_2012.prt
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

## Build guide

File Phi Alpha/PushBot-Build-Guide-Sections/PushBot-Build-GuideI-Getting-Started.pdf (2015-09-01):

# FIRST® Tech Challenge

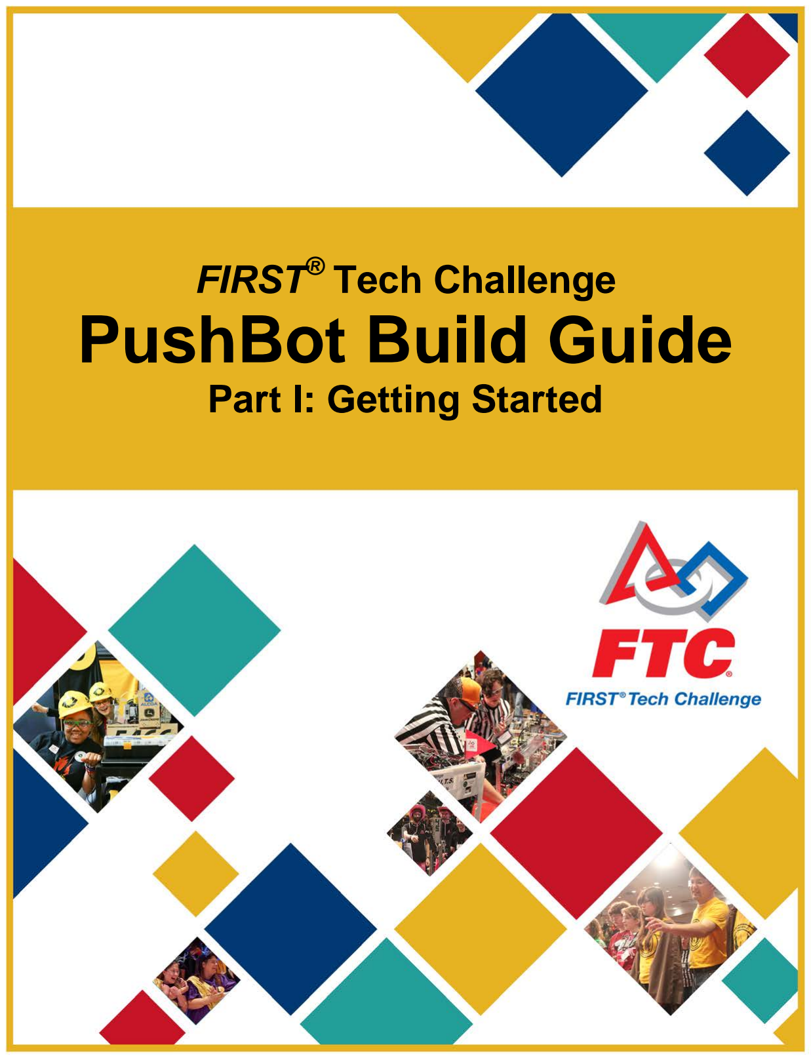
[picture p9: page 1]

# PushBot Build Guide

# Part I: Getting Started

2 | FIRST Tech Challenge PushBot Build Guide Part I: Getting Started

## Volunteer Thank You

Thank you for taking the time to volunteer for a FIRST Tech Challenge Event. FIRST and FTC rely heavily on Volunteers to ensure Events run smoothly and are a fun experience for Teams and their families, which could not happen without people like you. With over 4,500 Teams competing annually, your dedication and commitment are paramount to the success of each Event and the FTC program. Thank you for your time and effort in supporting the mission of FIRST!

## Sponsor Thank You

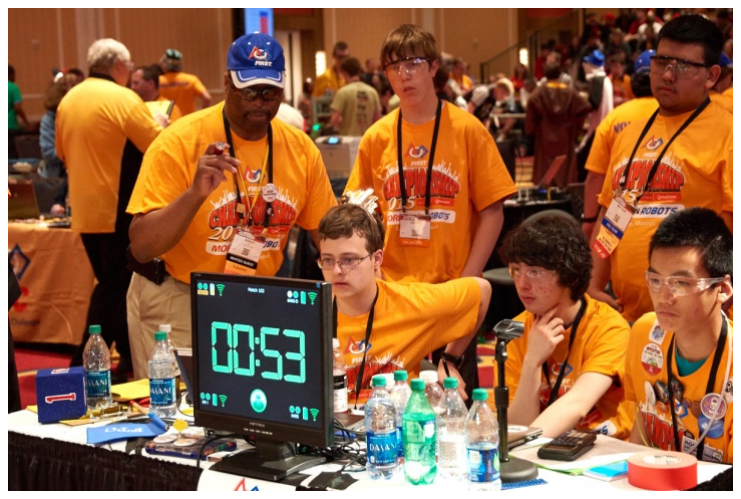
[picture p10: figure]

Thank you to our generous sponsors for your continued support of the FIRST Tech Challenge!

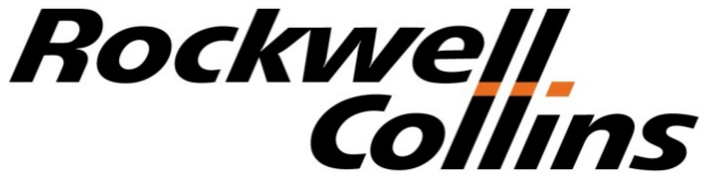
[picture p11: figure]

Official Program Sponsor

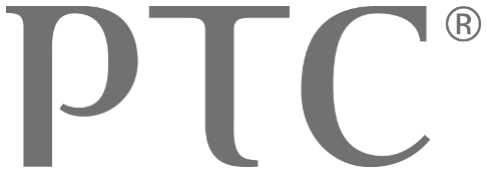
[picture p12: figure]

CAD and Collaboration Sponsor

FIRST Tech Challenge PushBot Build Guide Part I: Getting Started | 3

Revision History
Revision | Date | Description
1 | 8/15/2014 | Initial Release – by FTC Team #003 Australia, The Southport School
2 | 9/1/2014 | Replaced MATRIX with TETRIX content by former FTC Team #2843, Under the Son
3 | 8/6/2015 | Updated using the new kit of parts and new programming environment.

## Contents

4 | FIRST Tech Challenge PushBot Build Guide Part I: Getting Started

## Introduction

What is the FIRST Tech Challenge?
FIRST Tech Challenge is a student-centered activity that focuses on giving students a unique and stimulating experience. Each year, Teams participate in a new Game that requires them to design, build, test, and program autonomous and driver-operated Robots that must
perform a series of tasks.
The Playing Field for the Game consists of the FIRST Tech
Challenge Game Pieces set up on a foam-mat surface, surrounded by a metal and Lexan Field frame. Each Tournament features Alliances, which are comprised of two Teams, competing against one another on the Playing Field. Teams work to overcome obstacles and meet challenges, while learning from and interacting with their peers and adult Mentors. Students develop a greater appreciation of science and technology and how they might use that knowledge to impact the world around them in a positive manner. They also cultivate life skills such as:

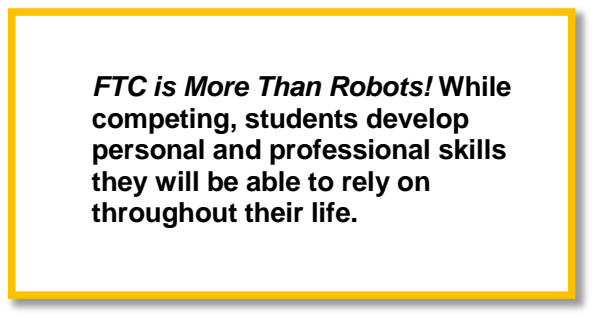
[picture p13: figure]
FTC is More Than Robots! While competing, students develop personal and professional skills they will be able to rely on throughout their life.

- Planning, brainstorming, and creative problem-solving.
- Research and technical skills.
- Collaboration and Teamwork.
- Appreciation of differences and respect for the ideas and contributions of others. To learn more about FTC and other FIRST Robotics competitions, visit www.usfirst.org.
FIRST Tech Challenge (FTC) Core Values
FIRST asks everyone who participates in FTC to uphold and promote the following values:
- We display Gracious Professionalism with everyone we engage with and in everything we do.
- We act with integrity.
- We have fun.
- We are a welcoming community of students,
mentors, and volunteers.
- What we learn is more important than what we win.
- We respect each other and celebrate our diversity.
- Students and adults work together to find solutions to challenges.
- We honor the spirit of friendly competition.
- We behave with courtesy and compassion for others at all times.
- We act as ambassadors for FIRST and the FIRST Tech Challenge.
- We inspire others to adopt these values.

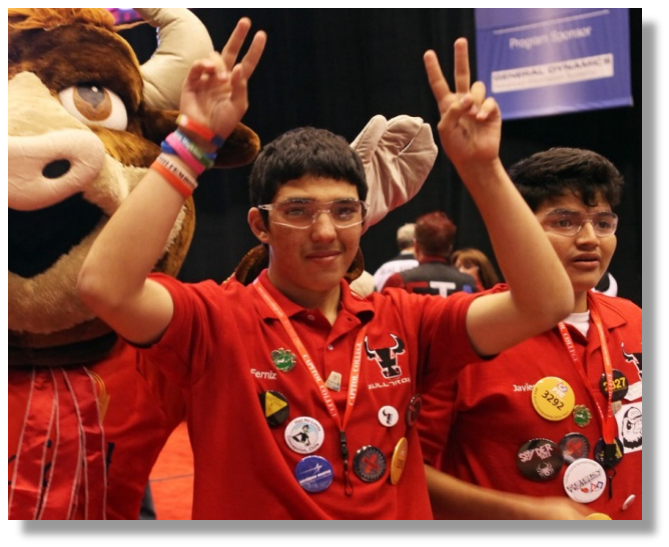
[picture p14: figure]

FIRST Tech Challenge PushBot Build Guide Part I: Getting Started | 5

## What is the FIRSTTech Challenge PushBot Build Guide?

In early 2014, a design challenge was set by FIRST for experienced FTC Teams to design a basic Robot and manual for Rookie FTC Teams. The Robot and manual had to provide Rookie Teams with simple, basic instructions and images for building a PushBot that can be successful in competition for any Game Challenge. PushBot 2 (PB2) needs to meet all FTC Competition guidelines using the current Game Manual and Forum rules, but using ONLY the Competition Kit of Parts and materials.
As part of the task, the PushBot needed to have basic programming for autonomous mode; as well as a program for manual mode. The code was to be developed in the Java programming language and deployed using the Android Studio IDE.
Depending on the Team size and student interests, some sections of this manual can be done in parallel. One group can build the Robot, while another group is installing the software, and a third group can build the electronics test bench. The efforts of these groups would come together during the wiring and testing portion. FTC Team #2843 United States – PushBot Robot.
2015 – 2016 Robot Name: PB2 (PushBot 2)
Purpose: Assist new FTC competitors to develop a sense of how an FTC Robot is constructed with the TETRIX Robotic Construction system and is programmed in Java.
Design: The PushBot has 3 DC motors and 2 servos. Its design is based around a rectangular frame. This allows structural engineering principles to be explored by Teams. The Robot has an ‘arm’ powered by a single DC motor, a ‘hand’ that is driven by two servos, and ‘feet’ powered by two DC motors. The ’arm’ is geared down to allow the DC motor to lift heavier objects. PB2
has high clearance for driving over objects. PB2 can
push objects using its gripper or a front panel can be
installed to ‘push’ objects. This Guide will assist rookie FTC competitors in gaining an understanding of how a simple Robot built with the TETRIX Construction System can be programmed in Java. It will also guide Teams through using the new electronics available in the 2015-2016 season.
The Robot is constructed with the TETRIX Kit of Parts and an electronics kit, which includes cell phones as the communication devices and other USB devices that provide communication with new USB modules. A link to the TETRIX Kit of Parts description is available on the FTC Team Resources webpage. (http://www.usfirst.org/roboticsprograms/ftc/team-resources)

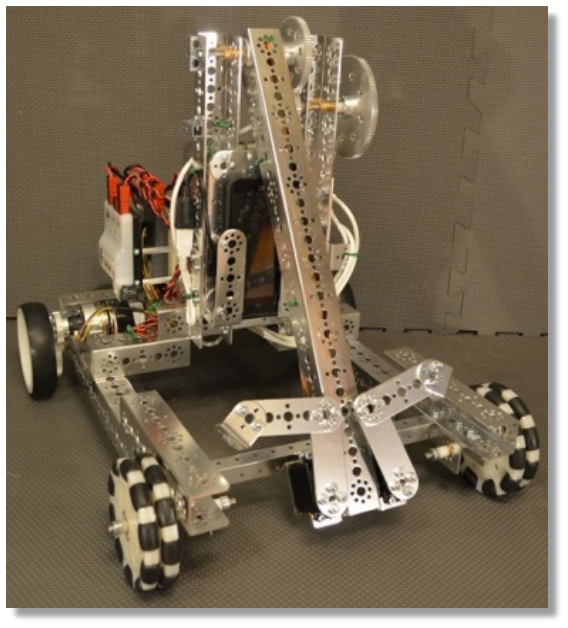
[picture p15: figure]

6 | FIRST Tech Challenge PushBot Build Guide Part I: Getting Started

## Gracious ProfessionalismTM

FIRST uses this term to describe the program’s intent. This is one of the most important concepts that can be taught to a young person who is learning to get along in the work world. At FIRST, Team members help other Team members, but they also help other Teams.
Gracious Professionalism is not clearly defined for a reason. It can and should mean different things to everyone.
Some possible meanings of Gracious Professionalism include:
- Gracious attitudes and behaviors are win-win.
- Gracious folks respect everyone and let that respect show in their actions.
- Professionals possess special knowledge and are trusted by society to use that knowledge responsibly.
- Gracious Professionals make a valued contribution in
a manner pleasing to others and to themselves.

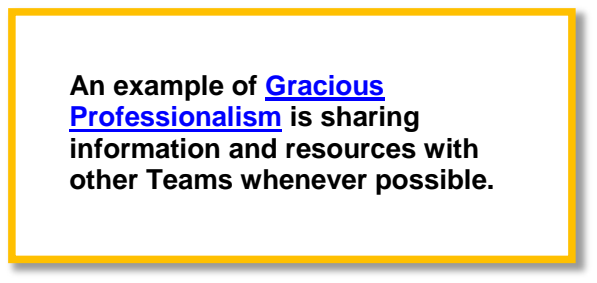
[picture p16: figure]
An example of Gracious Professionalism is sharing information and resources with other Teams whenever possible.

In the context of FIRST, this means that all Teams and participants should:
- Learn to be strong competitors, but also treat one another with respect and kindness in the process.
- Avoid leaving anyone feeling as if they are excluded or unappreciated.
- Knowledge, pride and empathy should be comfortably and genuinely blended.
In the end, Gracious Professionalism is part of pursuing a meaningful life. When professionals use knowledge in a Gracious manner and individuals act with integrity and sensitivity, everyone wins, and society benefits. Watch Dr. Woodie Flowers explain Gracious Professionalism in this short video. (https://www.youtube.com/watch?v=F8ZzoC9tCWg&list=UUkWMXdRQr5yoZRz7gFYyRcw)

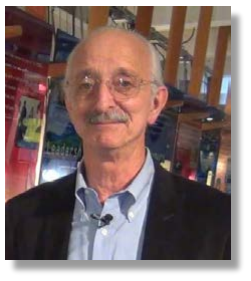
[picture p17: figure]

“The FIRST spirit encourages doing high-quality, well-informed work in a manner that leaves everyone feeling valued. Gracious Professionalism seems to be a good descriptor for part of the ethos of FIRST. It is part of what makes FIRST different and wonderful.”
- Dr. Woodie Flowers, National Advisor for FIRST

FIRST Tech Challenge PushBot Build Guide Part I: Getting Started | 7

## FIRST Youth Protection Program

The purpose of the FIRST Youth Protection Program (FIRST YPP) is to provide coaches, mentors, Volunteers, employees, others working in FIRST programs, Team members, parents, and guardians of Team members with information, guidelines, and procedures to create safe environments for everyone participating in FIRST programs. The FIRST YPP sets minimum standards recommended for all FIRST activities. Adults working in FIRST programs must be knowledgeable of the standards set by the FIRST YPP, as well as those set by the school or organization hosting their Team.
Youth Protection Expectations and Guidelines Coaches and Mentors are expected to read and follow elements in the FIRST Youth Protection Program guide (http://www.usfirst.org/sites/default/files/uploadedFiles/About_Us/FIRST-YPP-ProgramGuide.pdf) that are labeled as required are mandatory in the United States and Canada, and may not be waived without the approval of the FIRST Youth Protection Department.

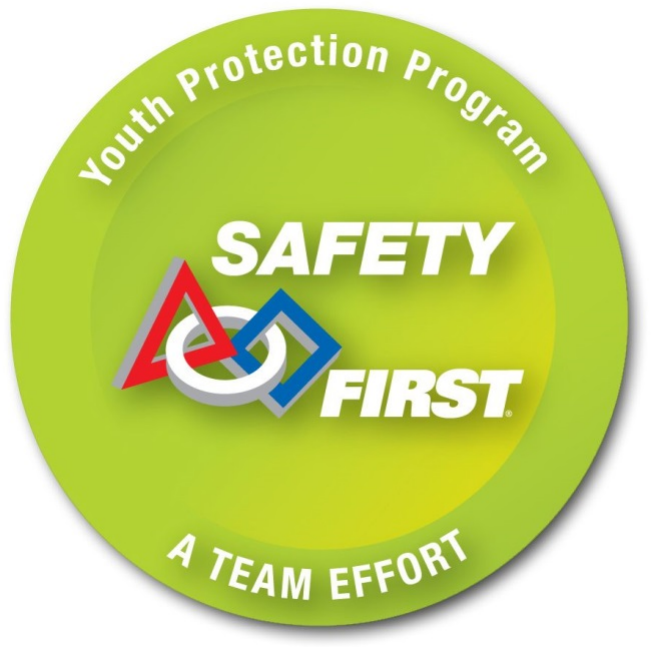
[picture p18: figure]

FIRST recommends that the standards set forth in the FIRST Youth Protection Program guide (http://www.usfirst.org/sites/default/files/uploadedFiles/About_Us/FIRST-YPP-ProgramGuide.pdf) be applied outside of the United States and Canada to the extent possible. At a minimum, local regulations regarding youth protection must be complied with. Forms are available here: http://www.usfirst.org/aboutus/youth-protection-program (http://www.usfirst.org/aboutus/youth-protection-program)
Information on the US Screening process is available here: http://www.usfirst.org/sites/default/files/uploadedFiles/About_Us/U

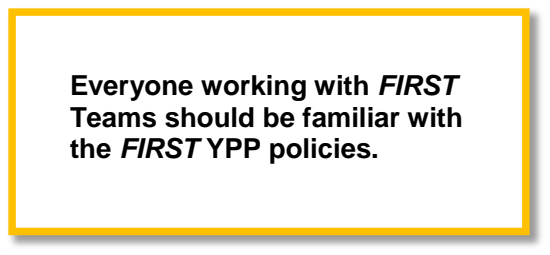
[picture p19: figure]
Everyone working with FIRST Teams should be familiar with the FIRST YPP policies.

S-Youth-Protection-Clearance-Process.pdf (http://www.usfirst.org/sites/default/files/uploadedFiles/About_Us/US-Youth-Protection-Clearance-Process.pdf)
Information on the Canadian Screening process is available here: http://www.usfirst.org/sites/default/files/uploadedFiles/About_Us/Canadian-Youth-Protection-Clearance.pdf You can find FAQ and additional information about the FIRST Youth Protection Program on the FIRST website at: http://www.usfirst.org/aboutus/youth-protection-program

NOTICE OF NON-DISCRIMINATION
United States Foundation for Inspiration and Recognition of Science and Technology (FIRST®) does not discriminate on the basis of race, color, national origin, sex, disability, or age in its programs and activities. The following person has been designated to handle inquiries regarding the non-discrimination policies: Lee Doucette, Youth Protection Program Manager, 200 Bedford Street, Manchester, NH 03101, 603-666-3906, Ext. 250.

8 | FIRST Tech Challenge PushBot Build Guide Part I: Getting Started

## Getting Started

This section of the PushBot Build Guide includes the Robot CAD Drawing and Appendices, including the Bill of Materials, for easy reference.
Robot CAD Drawing

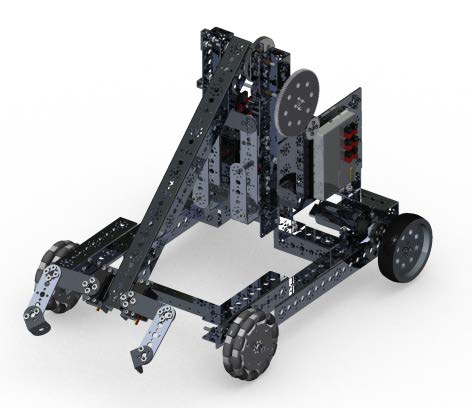
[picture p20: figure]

FIRST Tech Challenge PushBot Build Guide Part I: Getting Started | 9

# FIRST® Tech Challenge

# Mentor Manual

# Appendices

10 | FIRST Tech Challenge PushBot Build Guide Part I: Getting Started

## Appendix A: Bill of Materials List

This list does not include the cell phones and the cables that connect the electronics.
Quantity Name | Common Name
2 | CORE_MOTOR_CONTROLLER | Core Motor Controller
1 | CORE_POWER_DISTRIBUTION_MODULE Core Power Distribution Module
1 | CORE_SERVO_CONTROLLER | Core Servo Controller
12 | SCREW_SHCS_6-32_X_1_25_2011 | Gear Hub Screw
1 | TETRIX_731901_120_2013 | 120-Tooth Gear
3 | TETRIX_731903_2012 | Motor Power Wire
2 | TETRIX_736466_2012 | 4” Dual Omni Wheel Assembly
2 | TETRIX_738000_2012 | Motor Encoder
2 | TETRIX_738009_BATPACK_BRKT_2013 | Battery Clip
4 | TETRIX_739028_2012 | 40-Tooth Gear
2 | TETRIX_739055_2012 | 4" Wheel
1 | TETRIX_739057_2012 | Battery Pack
2 | TETRIX_739060_2012 | Single Standard Scale Servo Bracket
5 | TETRIX_739061_2012 | Flat Bracket
3 | TETRIX_739062_2012 | L Bracket
2 | TETRIX_739065_2012 | 32mm Channel
4 | TETRIX_739066_2012 | 96mm Channel
4 | TETRIX_739067_2012 | 160m Channel
4 | TETRIX_739068_2012 | 288mm Channel
1 | TETRIX_739069_2012 | 416mm Channel
1 | TETRIX_739071_2012 | 288mm Angle
1 | TETRIX_739072_2012 | 144mm Angle
3 | TETRIX_739073_2012 | Flat Building Plage
3 | TETRIX_739079_2012 | Motor Hub
3 | TETRIX_739083_2012 | TETRIX DC Motor
3 | TETRIX_739086_2012 | 80-Tooth Gear
6 | TETRIX_739088_2013 | Axel
3 | TETRIX_739089_2012 | DC Motor Mount
3 | TETRIX_739090_2012 | Gear Hub Spacer
17 | TETRIX_739091_2013 | Bronze Bushing
6 | TETRIX_739092_ 2012 | Axel Collar
162 | TETRIX_739094_2013 | Kep Nut
64 | TETRIX_739097_2013 | 1/2" Socket Head Cap Screw
86 | TETRIX_739098_2012 | 5/16" Socket Head Cap Screw
11 | TETRIX_739100_2012 | 1/8" Axel Spacer
3 | TETRIX_739101_2012 | 3/8" Axel Spacer
6 | TETRIX_739102_2012 | 1" Stand-off
4 | TETRIX_739107_2013 | 32mm Stand-off
42 | TETRIX_739111_2012 | Button Head Cap Screw
2 | TETRIX_739120_2012 | Hard Point Connector
5 | TETRIX_739172_ 2012 | Axel Hub
6 | TETRIX_739195_2012 | Motor Mount Screw
2 | TETRIX_739197_ 2012 | Standard-Scale HS-485HB Servo Motor
2 | TETRIX_739270_2013 | Inside C Connector

FIRST Tech Challenge PushBot Build Guide Part I: Getting Started | 11
3 | TETRIX_739272_2013 | 160mm Flat
4 | TETRIX_739273_2013 | 96mm Flat
4 | TETRIX_739281_CORNER_BRA_2013 | Inside Corner Bracket
1 | TETRIX_739387_2013 | 2mm Spacer
2 | 39081 | Servo Extension Wire

12 | FIRST Tech Challenge PushBot Build Guide Part I: Getting Started

## Appendix B: References

The right to use any unnumbered quoted text in this document has been graciously given by FIRST for use in this document. It may not be used outside of this document with the consent of FIRST.

## Appendix C: Project Team Profiles

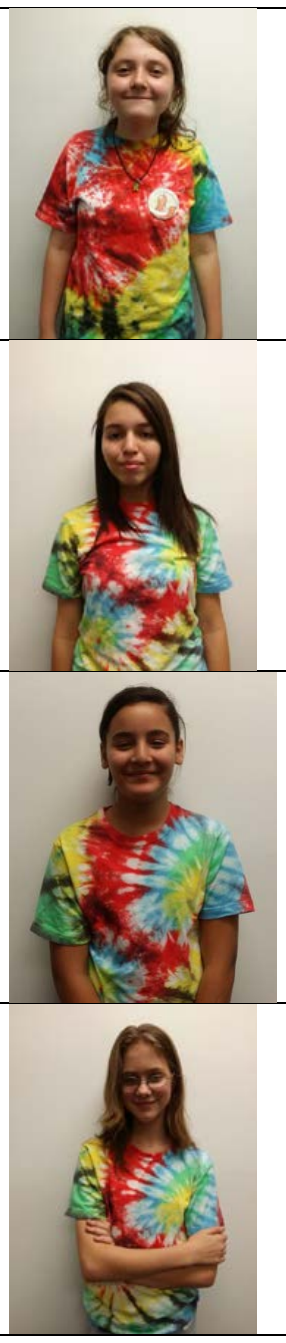
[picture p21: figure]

Isa Year 9 student at Great Mills High School. Student for 1 year on Team #2843, Under the Son

Alanis Year 9 student at Great Mills High School. Student for 1 year on Team #2843, Under the Son

Nanette Year 7 student at Esperanza Middle School. Student for 1 year on Team #2843, Under the Son

Laura Year 9 student at Leonardtown High School. Student for 7 years on Team #2843, Under the Son

FIRST Tech Challenge PushBot Build Guide Part I: Getting Started | 13

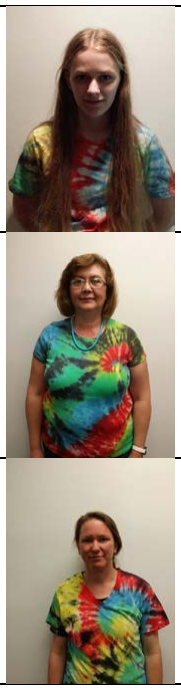
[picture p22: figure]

Mary Year 12 student at Leonardtown High School. Student for 7 years on Team #2843, Under the Son Volunteer for 7 years, MD FIRST

Claudia Mentor for 1 year on Team #2843, Under the Son

Lydean Coach for 7 years on Team #2843, Under the Son Volunteer for 7 years, MD FIRST ssi@the-spanglers.net

David Mentor for 7 years on Team #2843, Under the Son Volunteer for 7 years, MD FIRST ssi@the-spanglers.net

14 | FIRST Tech Challenge PushBot Build Guide Part I: Getting Started

## Appendix D: Resources & Support

FTC Game Manuals – Part I and II - http://www.usfirst.org/roboticsprograms/ftc/Game FIRST Headquarters Support
Phone: 603-666-3906 or toll free 800-871-8326
Email: FTCTeams@usfirst.org
USFIRST.ORG
FIRST Tech Challenge (FTC) Webpage (http://www.usfirst.org/roboticsprograms/ftc/volunteer-resources) – For everything FTC.
FTC Season Timeline (http://www3.usfirst.org/whats-going-on) – Find FTC Events in your area.
FTC Forum (http://ftcforum.usfirst.org/forum.php) – to ask questions about the annual game challenge and participate in information sharing. FIRST Championship Conferences webpage – for archived presentations and materials

FIRST Tech Challenge Social Media
FTC Twitter Feed (https://twitter.com/FTCTeams) - If you are on Twitter, follow the FTC twitter feed for news updates.
FTC Facebook page (https://www.facebook.com/FTCTeams) - If you are on Facebook, follow the FTC page for news updates.
FTC YouTube Channel (https://www.youtube.com/user/FIRSTTechChallenge) – Contains training videos, Game animations, news clips, and more.
FTC Blog (http://firsttechchallenge.blogspot.com/) – Weekly articles for the FTC community, including Outstanding Volunteer Recognition! FTC Team Email Blasts (http://www.usfirst.org/roboticsprograms/ftc/emailblastarchive.aspx) – contain the most recent FTC news for Teams.
FTC Google+ (https://plus.google.com/100910548536794889930/posts) community - If you are on Google+, follow the FTC community for news updates.

Android-Based Technology Support
FTC Technology Forum (http://ftcforum.usfirst.org/forumdisplay.php?156-FTC-Technology)
FTC Technology Webpage (http://www.usfirst.org/roboticsprograms/ftc/technology)
FTC Team Resources Webpage (http://www.usfirst.org/roboticsprograms/ftc/team-resources)
Product Support
FIRST will handle questions about Team registration, grants, Events, and Affiliate Partners. Pitsco will handle questions about ordering, payment, and delivery of competition sets and materials.
- U.S. & Canada: 800-835-0686 FREE
- Outside U.S. and Canada: 620-231-0100
- U.S. Fax: 800-533-8104

## Feedback

We strive to create support materials that are the best they can be. If you have feedback regarding this manual, please email ftcteams@usfirst.org. Thank you!

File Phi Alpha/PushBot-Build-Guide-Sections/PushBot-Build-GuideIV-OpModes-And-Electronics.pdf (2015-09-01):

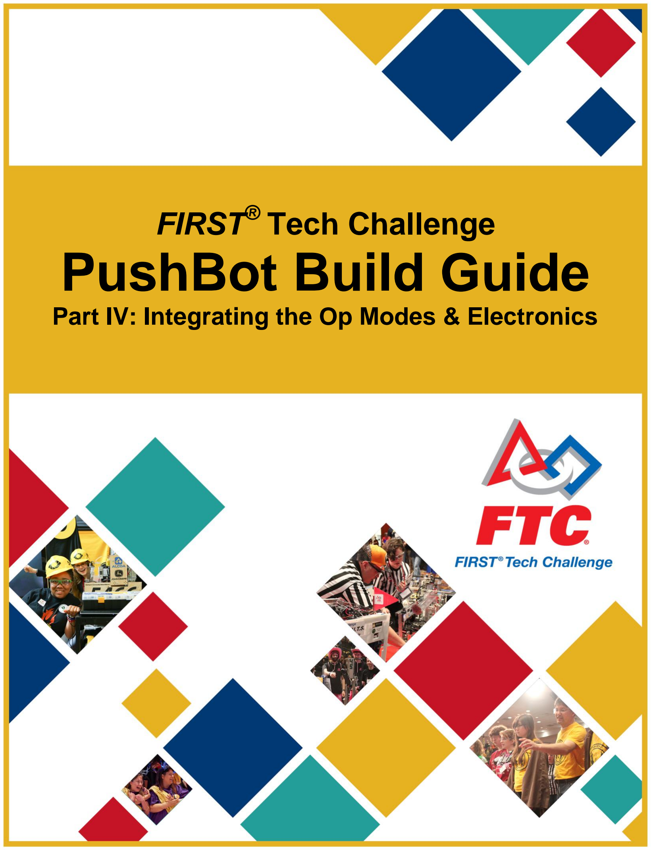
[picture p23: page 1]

# FIRST® Tech Challenge

# PushBot Build Guide

# Part IV: Integrating the Op Modes & Electronics

2 | FIRST Tech Challenge PushBot Build Guide Part IV: Integrating the Op Modes and Electronics

Revision History
Revision | Date | Description
1 | 8/15/2014 | Initial Release – by FTC Team #003 Australia, The Southport School
2 | 9/1/2014 | Replaced MATRIX with TETRIX content by former FTC Team #2843, Under the Son
3 | 8/6/2015 | Updated using the new kit of parts and new programming environment.

### Contents

FIRST Tech Challenge PushBot Build Guide Part IV: Integrating the Op Modes and Electronics | 3

### Integrating the Op modes and Electronics

From previous steps, the Driver Station and Robot Controller apps have been installed on the cell phones. The cell phones are powered on and the apps have been started. When the Robot Controller app configures the USB devices, the devices are assigned randomly – the order depends on which control responds to the query first. This means that sometimes when the devices are first scanned, motor ‘A’ is named Motor Controller 1, Motor Controller 2 or Motor Controller 3 - the numbers are assigned 1 to the number of USB devices, not the number of motor controllers. This section will determine which motor controller operates the wheels and which operates the arm. Once the USB devices are named the serial number of the device is used to control communication, not the order in which the devices are discovered.

Building the electronics test bench
This section will outline the testing of the electronics to determine which motor controller will be used to control the drive wheel motors and which will control the arm motor. This step happens prior to attaching the electronics to the Robot. Here is a picture showing the electronics that will be mounted to the Robot. Note: parts may vary slightly in appearance to what is shown.

The instructions in this section apply to the Robot Controller cell phone only.

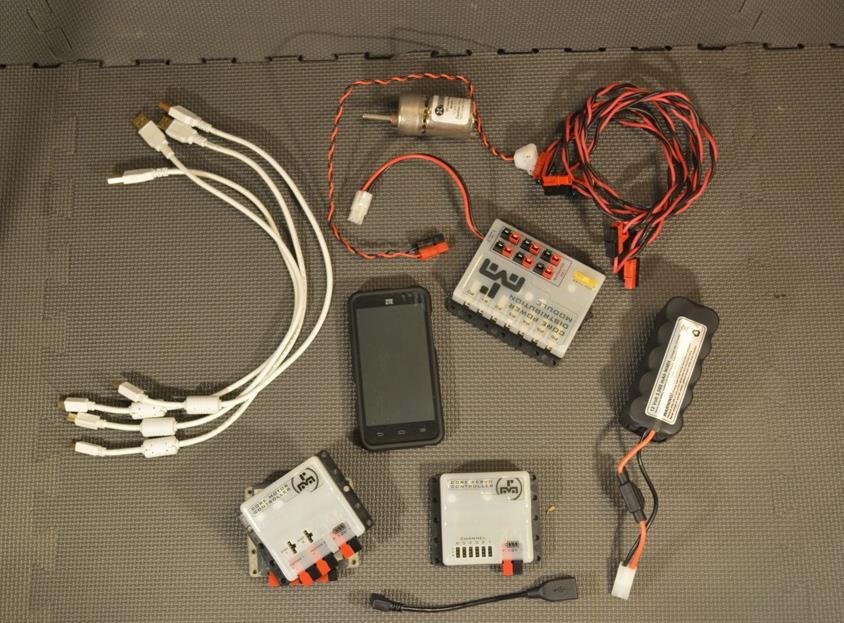
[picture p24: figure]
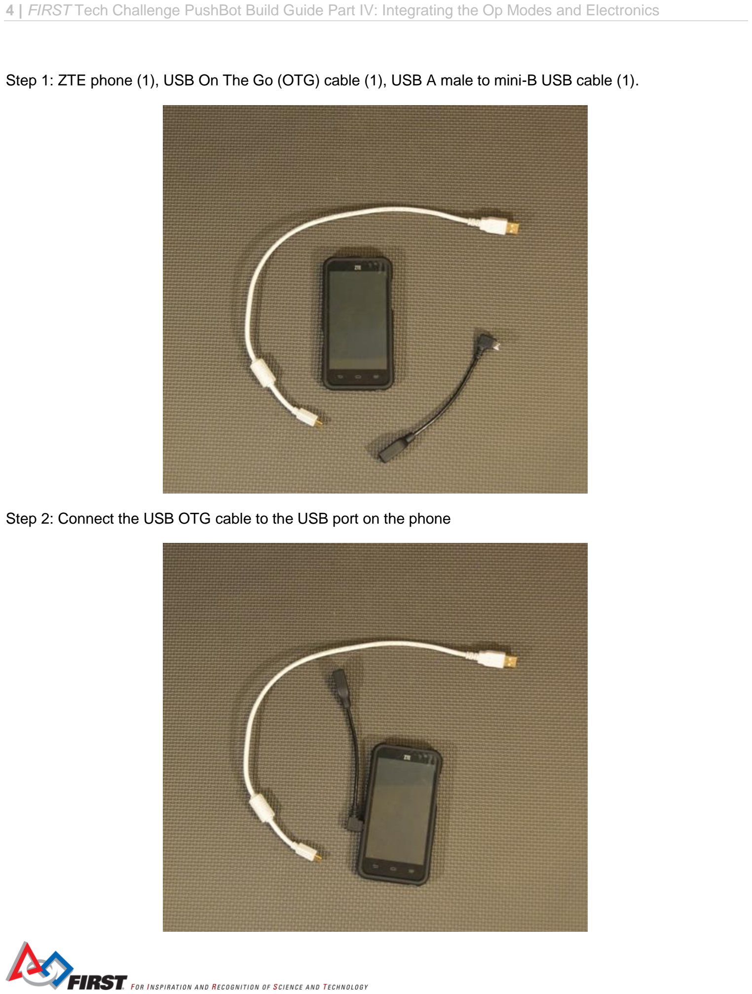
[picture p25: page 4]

4 | FIRST Tech Challenge PushBot Build Guide Part IV: Integrating the Op Modes and Electronics
Step 1: ZTE phone (1), USB On The Go (OTG) cable (1), USB A male to mini-B USB cable (1).
Step 2: Connect the USB OTG cable to the USB port on the phone

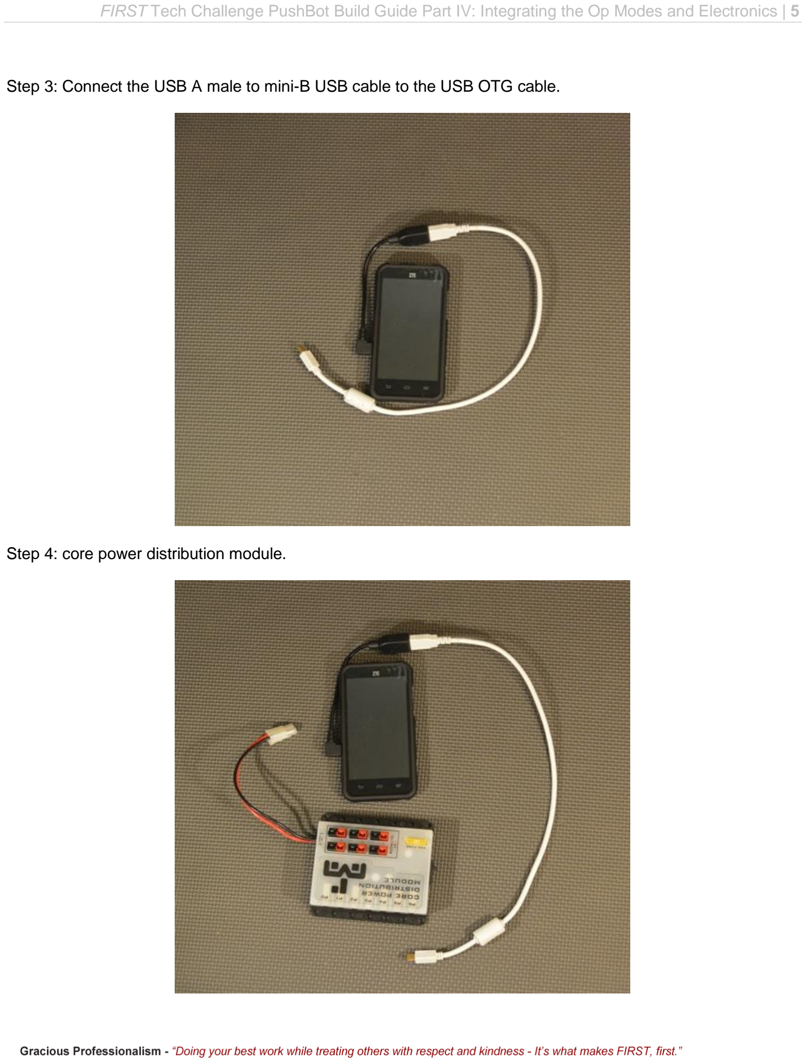
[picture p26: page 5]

FIRST Tech Challenge PushBot Build Guide Part IV: Integrating the Op Modes and Electronics | 5
Step 3: Connect the USB A male to mini-B USB cable to the USB OTG cable.
Step 4: core power distribution module.

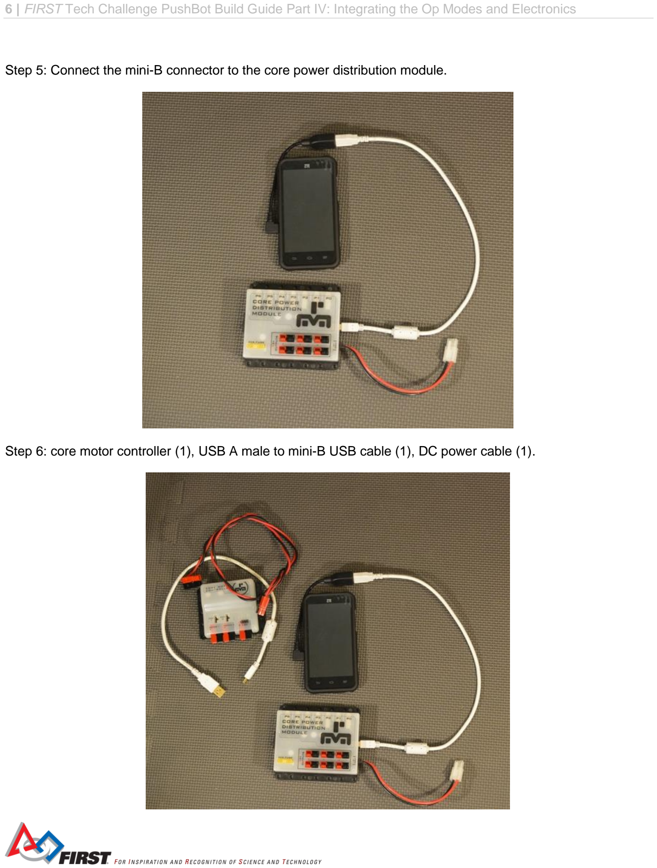
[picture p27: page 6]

6 | FIRST Tech Challenge PushBot Build Guide Part IV: Integrating the Op Modes and Electronics
Step 5: Connect the mini-B connector to the core power distribution module.
Step 6: core motor controller (1), USB A male to mini-B USB cable (1), DC power cable (1).

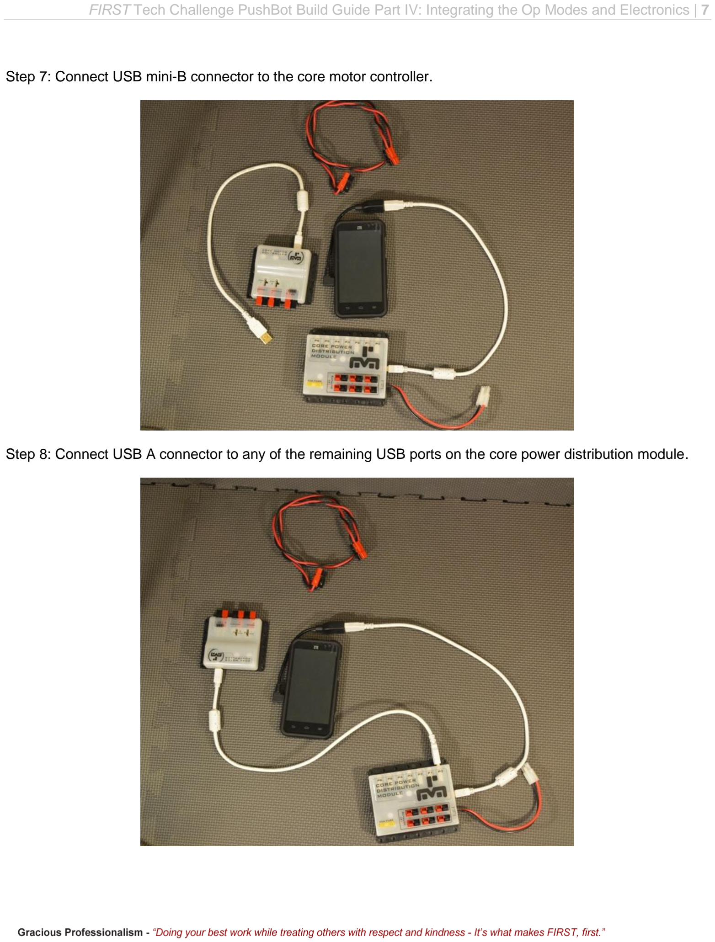
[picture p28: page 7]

FIRST Tech Challenge PushBot Build Guide Part IV: Integrating the Op Modes and Electronics | 7
Step 7: Connect USB mini-B connector to the core motor controller.
Step 8: Connect USB A connector to any of the remaining USB ports on the core power distribution module.

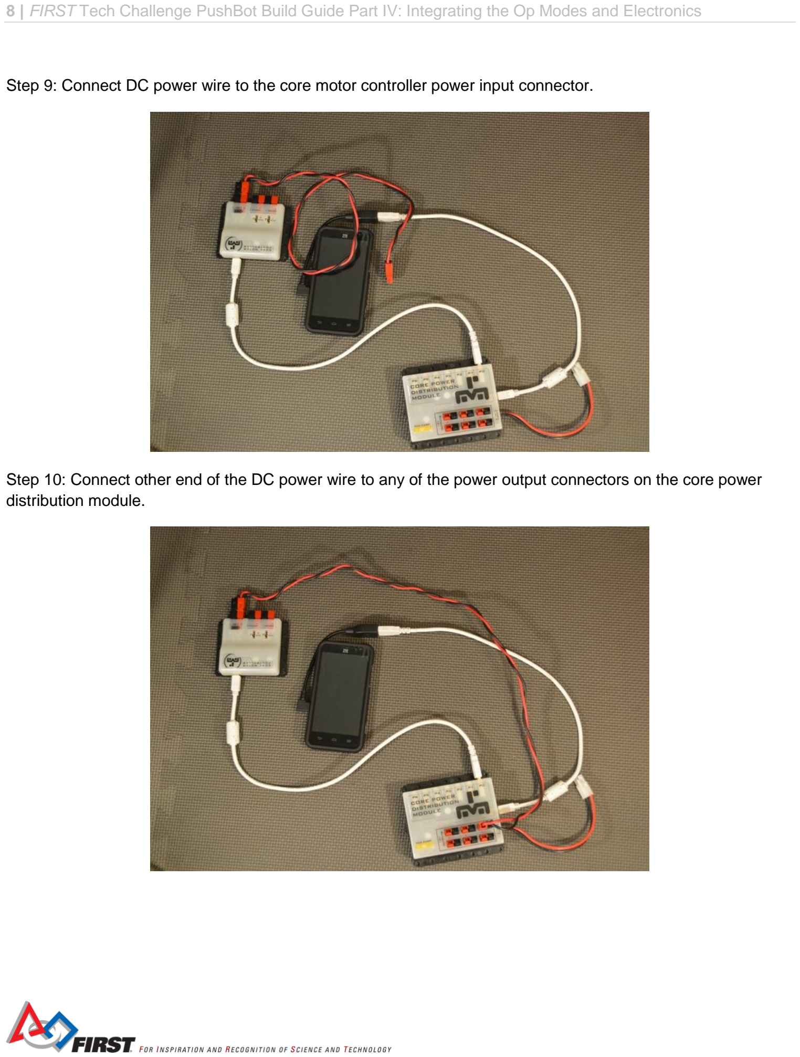
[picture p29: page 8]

8 | FIRST Tech Challenge PushBot Build Guide Part IV: Integrating the Op Modes and Electronics
Step 9: Connect DC power wire to the core motor controller power input connector.
Step 10: Connect other end of the DC power wire to any of the power output connectors on the core power distribution module.

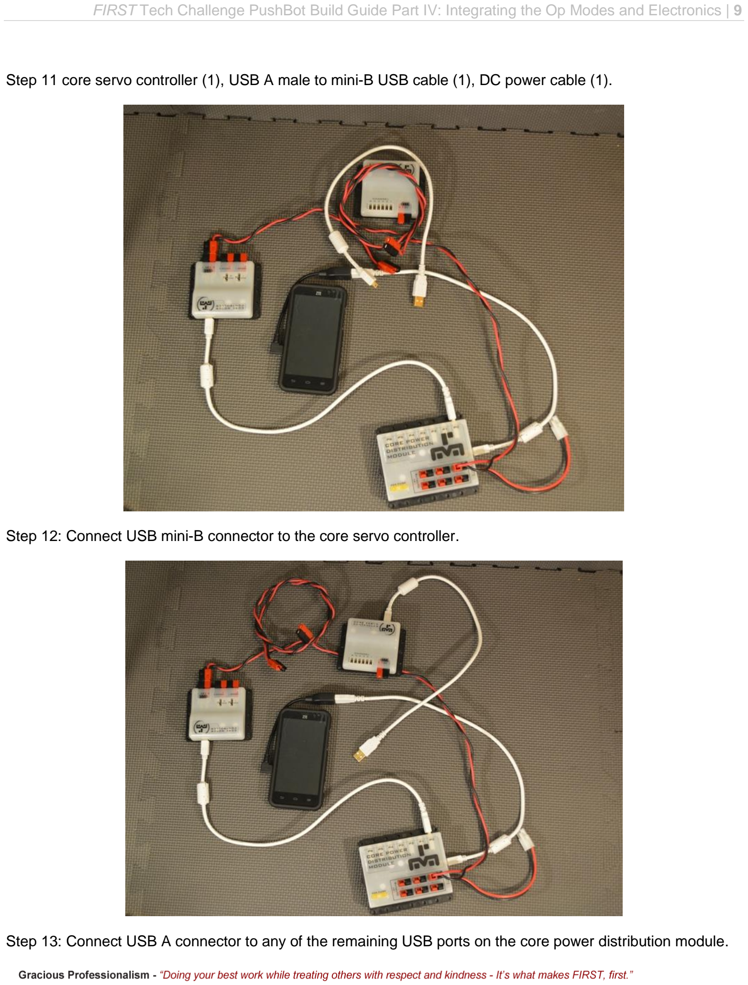
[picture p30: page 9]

FIRST Tech Challenge PushBot Build Guide Part IV: Integrating the Op Modes and Electronics | 9
Step 11 core servo controller (1), USB A male to mini-B USB cable (1), DC power cable (1).
Step 12: Connect USB mini-B connector to the core servo controller.
Step 13: Connect USB A connector to any of the remaining USB ports on the core power distribution module.

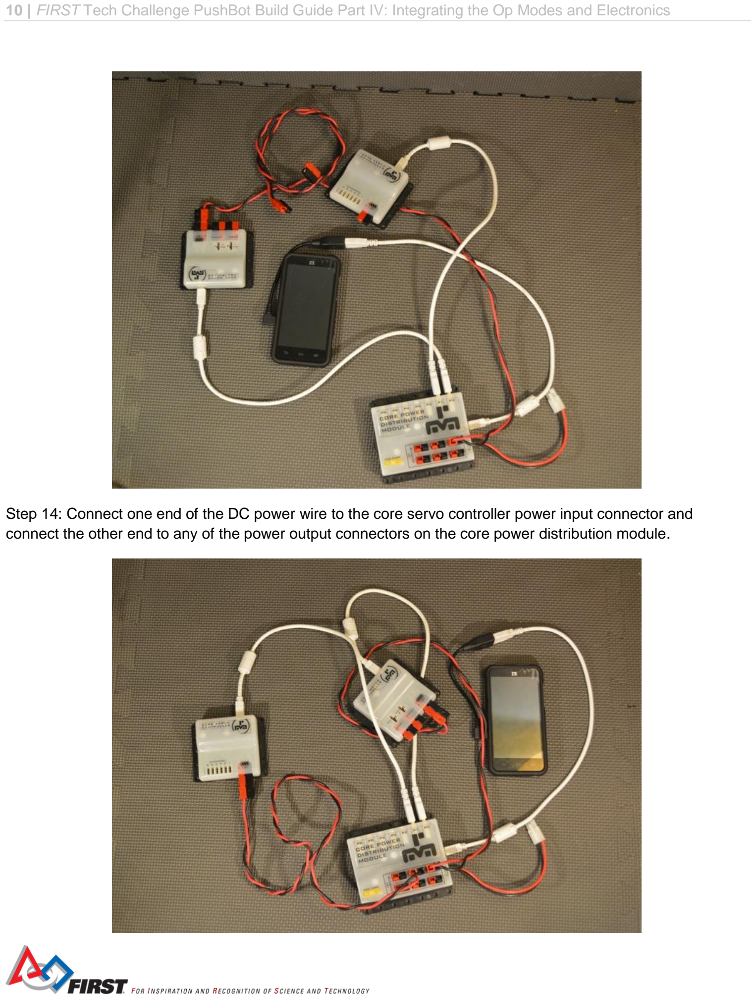
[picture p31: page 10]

10 | FIRST Tech Challenge PushBot Build Guide Part IV: Integrating the Op Modes and Electronics
Step 14: Connect one end of the DC power wire to the core servo controller power input connector and connect the other end to any of the power output connectors on the core power distribution module.

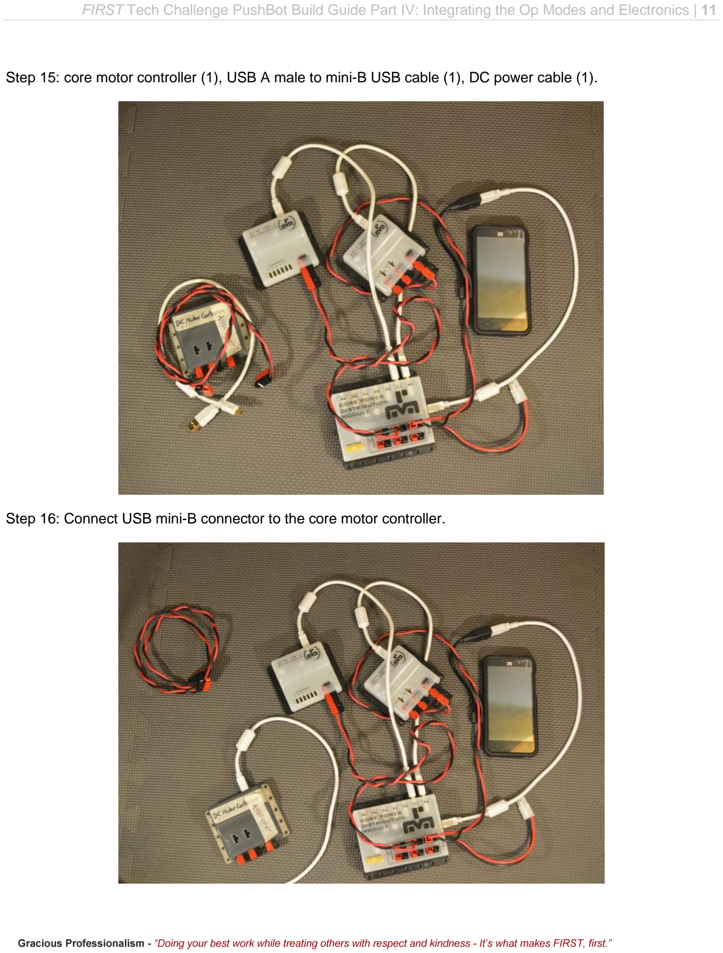
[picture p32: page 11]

FIRST Tech Challenge PushBot Build Guide Part IV: Integrating the Op Modes and Electronics | 11
Step 15: core motor controller (1), USB A male to mini-B USB cable (1), DC power cable (1).
Step 16: Connect USB mini-B connector to the core motor controller.

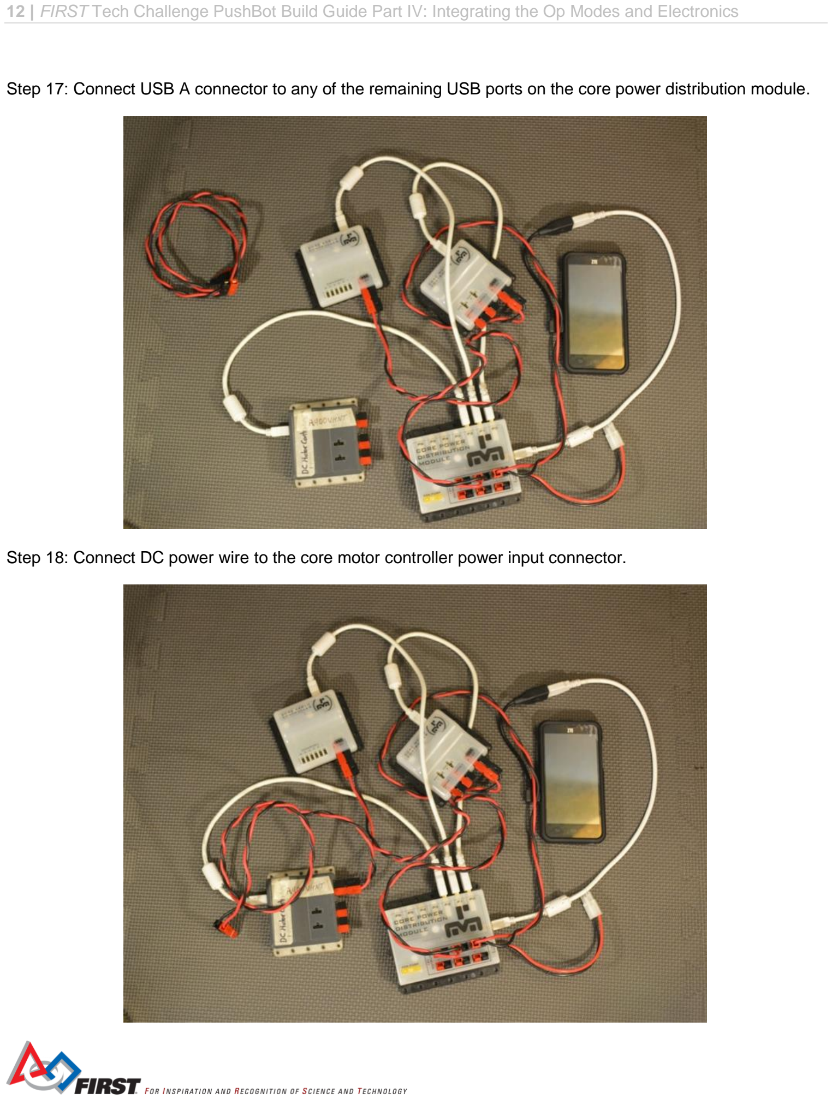
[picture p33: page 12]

12 | FIRST Tech Challenge PushBot Build Guide Part IV: Integrating the Op Modes and Electronics
Step 17: Connect USB A connector to any of the remaining USB ports on the core power distribution module.
Step 18: Connect DC power wire to the core motor controller power input connector.

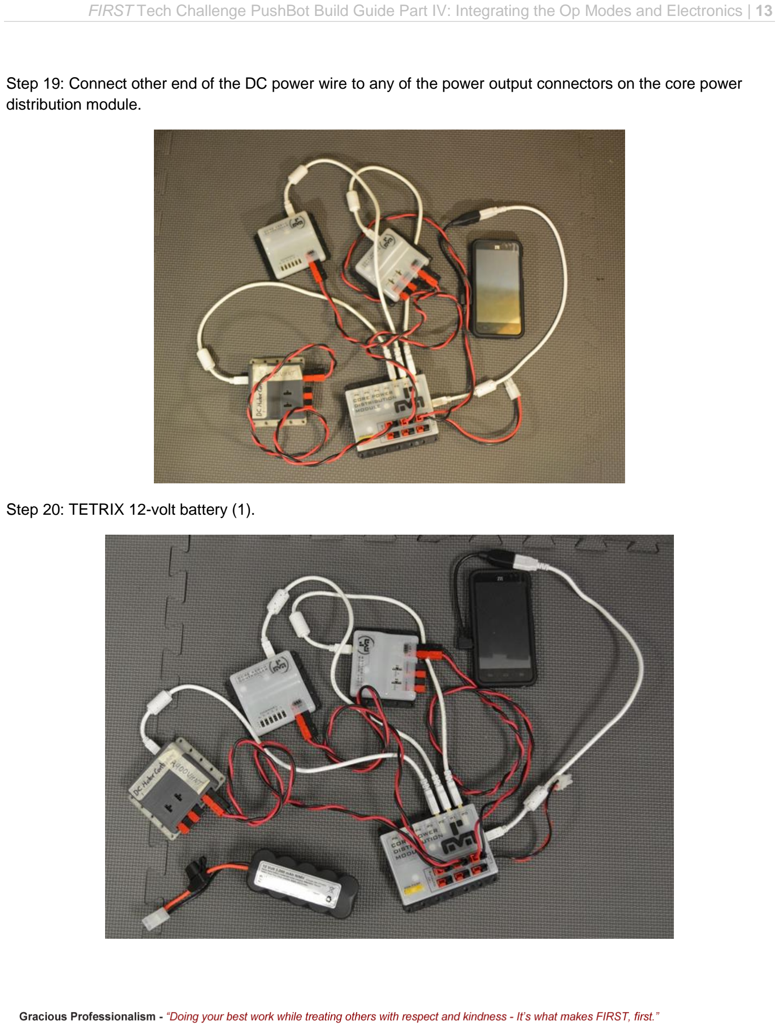
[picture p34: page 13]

FIRST Tech Challenge PushBot Build Guide Part IV: Integrating the Op Modes and Electronics | 13
Step 19: Connect other end of the DC power wire to any of the power output connectors on the core power distribution module.
Step 20: TETRIX 12-volt battery (1).

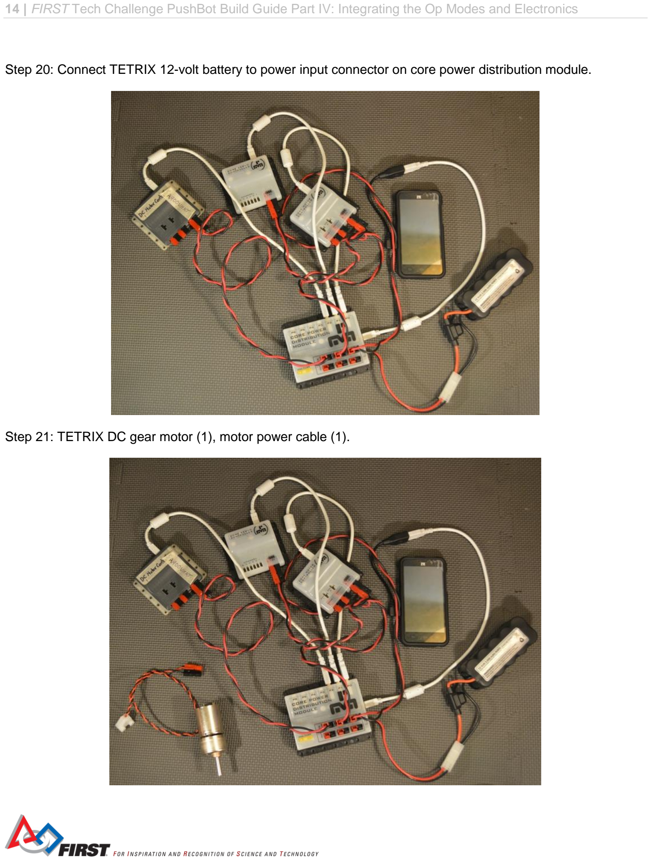
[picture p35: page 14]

14 | FIRST Tech Challenge PushBot Build Guide Part IV: Integrating the Op Modes and Electronics
Step 20: Connect TETRIX 12-volt battery to power input connector on core power distribution module.
Step 21: TETRIX DC gear motor (1), motor power cable (1).

FIRST Tech Challenge PushBot Build Guide Part IV: Integrating the Op Modes and Electronics | 15
Step 22: Connect motor power cable to DC gear motor.

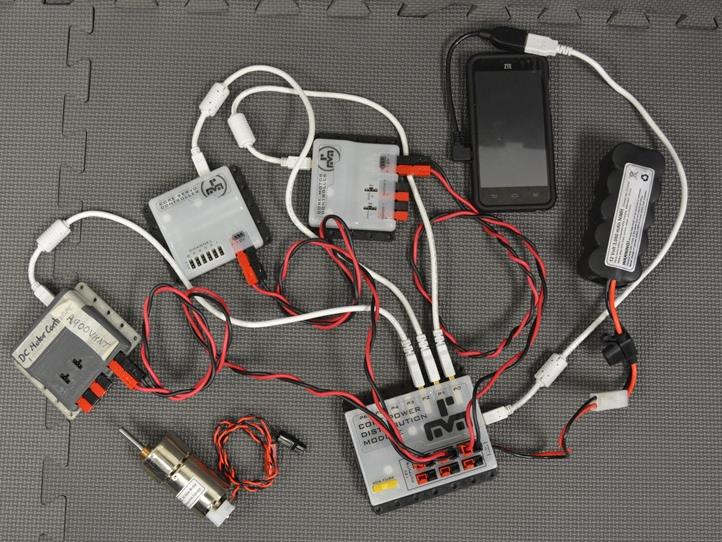
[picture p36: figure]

16 | FIRST Tech Challenge PushBot Build Guide Part IV: Integrating the Op Modes and Electronics

Configuring the USB devices
The Robot Controller app scans the devices connected to the Core Power Distribution Module. It builds a list of connected devices. To make the devices usable by an op-mode, they must be named. There is no identifying information provided via the interface, so a manual determination is required.
Step 1: Turn the core power distribution module on. The switch is on the side away from the power cable.

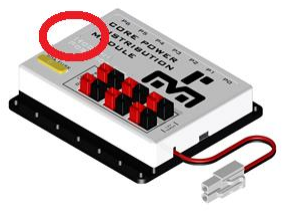
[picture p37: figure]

Step 2: When the core power distribution module is powered on, the Robot Controller app should auto-start (the home screen is replaced by the FTC Robot Controller activity) and may prompt the user to “remember” whether it can auto-start when the core power distribution module is detected in the future. Check the box to auto-start. Select ‘OK’. If this page is not being shown, then continue to the next step.

FIRST Tech Challenge PushBot Build Guide Part IV: Integrating the Op Modes and Electronics | 17
Step 3: Touch the overflow settings icon (three dots in the top right corner) to open a menu.

18 | FIRST Tech Challenge PushBot Build Guide Part IV: Integrating the Op Modes and Electronics
Step 4: Select settings.

FIRST Tech Challenge PushBot Build Guide Part IV: Integrating the Op Modes and Electronics | 19
Step 5: Select ‘Configure Robot’.

20 | FIRST Tech Challenge PushBot Build Guide Part IV: Integrating the Op Modes and Electronics
Step 6: Select ‘New’.

FIRST Tech Challenge PushBot Build Guide Part IV: Integrating the Op Modes and Electronics | 21
Step 7: Select ‘Scan’.

22 | FIRST Tech Challenge PushBot Build Guide Part IV: Integrating the Op Modes and Electronics
Step 8: If this dialog is shown, then check the box to allow
the app to access the USB device by default and select ‘OK’. If it isn’t shown, then continue to the next step.

FIRST Tech Challenge PushBot Build Guide Part IV: Integrating the Op Modes and Electronics | 23
Step 9: Select ‘Scan’ and the app will build a list of connected devices. Multiple scans may be required until the two motor controllers and one servo controller appear in the list.

24 | FIRST Tech Challenge PushBot Build Guide Part IV: Integrating the Op Modes and Electronics
Step 10: Select one of the motor controllers; it doesn’t matter which one.

FIRST Tech Challenge PushBot Build Guide Part IV: Integrating the Op Modes and Electronics | 25
Step 11: Tap on the Motor Controller’s name. It is the text just above “Enter the name for this motor controller here”. Using the keyboard, enter ‘drive_controller’.Long holding the ‘f’ character will insert the underscore between left and drive.

26 | FIRST Tech Challenge PushBot Build Guide Part IV: Integrating the Op Modes and Electronics
Step 12: Check the box next to 1. Tap on the text “NO
DEVICE ATTACHED”. Using the keyboard, enter ‘left_drive’. This must be exact or the Op mode will not work.

FIRST Tech Challenge PushBot Build Guide Part IV: Integrating the Op Modes and Electronics | 27
Step 13: Check the box next to 2. Using the keyboard, enter ‘right_drive’. This must be exact or the Op mode will not work.

28 | FIRST Tech Challenge PushBot Build Guide Part IV: Integrating the Op Modes and Electronics
Step 14: The screen should appear as it does below.
Select ‘Done’.

FIRST Tech Challenge PushBot Build Guide Part IV: Integrating the Op Modes and Electronics | 29
Step 15: Select the other motor controller.

30 | FIRST Tech Challenge PushBot Build Guide Part IV: Integrating the Op Modes and Electronics
Step 16: Tap on the Motor Controller’s name. It is the text
just above “Enter the name for this motor controller here”. Using the keyboard, enter ‘arm_controller’.

FIRST Tech Challenge PushBot Build Guide Part IV: Integrating the Op Modes and Electronics | 31
Step 17: Check the box next to 1. Using the keyboard, enter ‘left_arm’. This must be exact or the Op mode will not work.

32 | FIRST Tech Challenge PushBot Build Guide Part IV: Integrating the Op Modes and Electronics
Step 18: Select ‘Done’.

FIRST Tech Challenge PushBot Build Guide Part IV: Integrating the Op Modes and Electronics | 33
Step 19: Tap on the Servo Controller’s name. It is the text just above “Enter the name for this servo controller here”. Using the keyboard, enter ‘servo_controller’.

34 | FIRST Tech Challenge PushBot Build Guide Part IV: Integrating the Op Modes and Electronics
Step 20: Check the box next to 1. Using the keyboard,
enter ‘left_hand’. This must be exact or the Op mode will not work.

FIRST Tech Challenge PushBot Build Guide Part IV: Integrating the Op Modes and Electronics | 35
Step 21: Check the box next to 2. Using the keyboard, enter ‘right_hand’. This must be exact or the Op mode will not work.

36 | FIRST Tech Challenge PushBot Build Guide Part IV: Integrating the Op Modes and Electronics
Step 22: Select ‘Done’.

FIRST Tech Challenge PushBot Build Guide Part IV: Integrating the Op Modes and Electronics | 37
Step 23: Note that all of the devices have new names. Select ‘Save Configuration’.

38 | FIRST Tech Challenge PushBot Build Guide Part IV: Integrating the Op Modes and Electronics
Step 24: A pop-up will be displayed (left). Enter ‘push_bot’
as the file name. Select ‘OK’.

FIRST Tech Challenge PushBot Build Guide Part IV: Integrating the Op Modes and Electronics | 39
Step 25: Use the phone’s back button to return to the page shown on the left. Notice that the push_bot configuration is the ‘Active Configuration File’ (top right on the page). Also note that it is displayed as an available file.

40 | FIRST Tech Challenge PushBot Build Guide Part IV: Integrating the Op Modes and Electronics
Step 26: Use the phone’s back button to show the page on
the right.

FIRST Tech Challenge PushBot Build Guide Part IV: Integrating the Op Modes and Electronics | 41
Step 27: Use the phone’s back button to show the page on the left.

42 | FIRST Tech Challenge PushBot Build Guide Part IV: Integrating the Op Modes and Electronics

Assigning Gamepads
Two Logitech F310 gamepads will be connected to the Driver Station cell phone. These gamepads will be used by students to control a Robot’s functionality. The Driver Station app must configure the gamepads before they can be used.

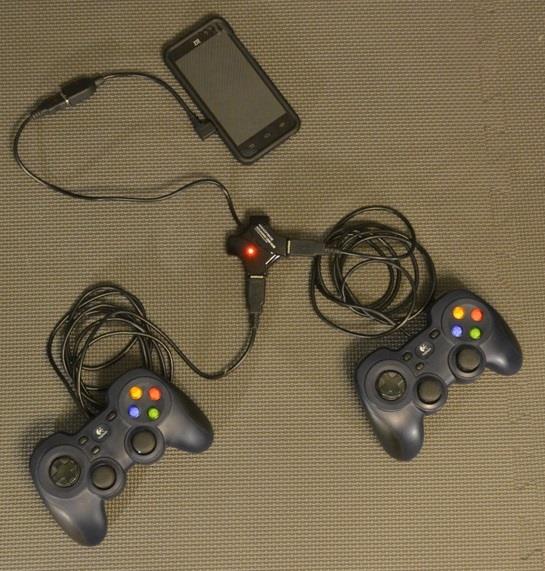
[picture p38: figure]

Step 1: Set the switch on the bottom of both gamepads to the “X” position.
Step 2: Select a gamepad that will be used as driver 1. Push the Start key on the gamepad while simultaneously pressing the A button.

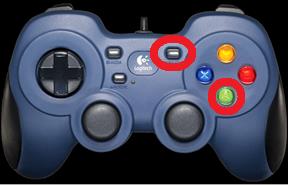
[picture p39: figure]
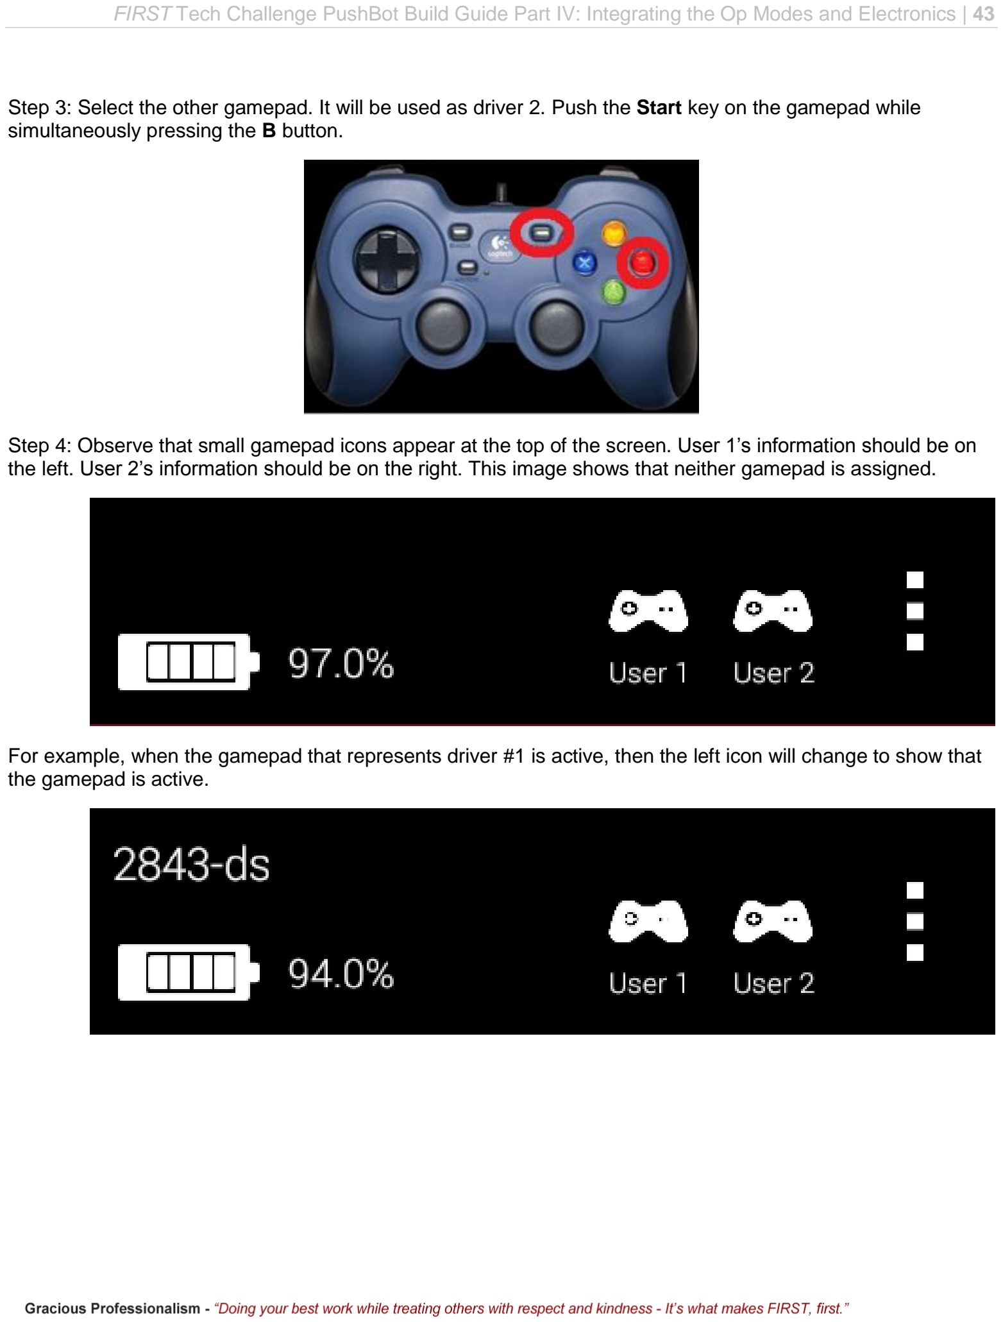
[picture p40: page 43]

FIRST Tech Challenge PushBot Build Guide Part IV: Integrating the Op Modes and Electronics | 43
Step 3: Select the other gamepad. It will be used as driver 2. Push the Start key on the gamepad while simultaneously pressing the B button.
Step 4: Observe that small gamepad icons appear at the top of the screen. User 1’s information should be on the left. User 2’s information should be on the right. This image shows that neither gamepad is assigned.

For example, when the gamepad that represents driver #1 is active, then the left icon will change to show that the gamepad is active.

44 | FIRST Tech Challenge PushBot Build Guide Part IV: Integrating the Op Modes and Electronics

If the gamepad that represents driver #2 is active, then the right icon will change.

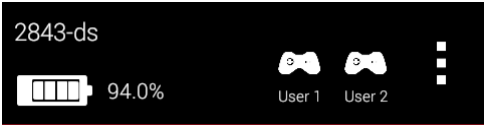
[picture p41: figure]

Note that for the joysticks on the gamepads, the values range from -1 to +1. For the x axis, -1 represents the far left range of motion and +1 represents the far right range. For the y axis -1 represents the topmost position and +1 represents the bottommost position.

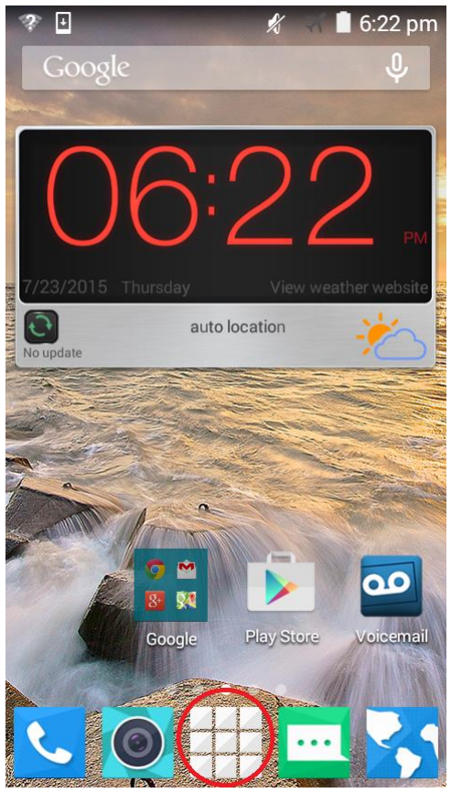
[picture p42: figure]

Pairing the Driver Station to the Robot Controller
The Driver Station app must first “pair” to the Robot controller to provide communication between the Robot and the gamepads.
Step 1: Power both cell phones on. Open the app drawer if the FTC Driver Station icon is not present on the main screen.

FIRST Tech Challenge PushBot Build Guide Part IV: Integrating the Op Modes and Electronics | 45
Step 2: Start the Driver Station app on the Driver Station cell phone.

46 | FIRST Tech Challenge PushBot Build Guide Part IV: Integrating the Op Modes and Electronics
Step 3: The screen on the right should be displayed on the
Driver Station cell phone.

FIRST Tech Challenge PushBot Build Guide Part IV: Integrating the Op Modes and Electronics | 47
Step 4: Make sure the Robot Controller app is running on the Robot Controller cell phone.

48 | FIRST Tech Challenge PushBot Build Guide Part IV: Integrating the Op Modes and Electronics
Step 4: On the Driver Station app touch the three vertical
dots on the upper right hand corner and select “Settings” from the pop up menu.

FIRST Tech Challenge PushBot Build Guide Part IV: Integrating the Op Modes and Electronics | 49
Step 5: Press the “Pair with Robot Controller” option to start the pairing process.

50 | FIRST Tech Challenge PushBot Build Guide Part IV: Integrating the Op Modes and Electronics
Step 6: After the previous step, the Driver Station will
display the following screen. Select the device.

FIRST Tech Challenge PushBot Build Guide Part IV: Integrating the Op Modes and Electronics | 51
Step 7: Use the back button to send a connection request to the Robot Controller.

52 | FIRST Tech Challenge PushBot Build Guide Part IV: Integrating the Op Modes and Electronics
Step 8: If this is the first pairing attempt, the Robot
Controller device might display a prompt asking if it is OK to allow an Android device to establish a Wi-Fi Direct connection. Select ‘Accept’.

FIRST Tech Challenge PushBot Build Guide Part IV: Integrating the Op Modes and Electronics | 53
Step 9: Observe that some of the controls on the display have changed indicating that the Driver Station is now connected to a Robot Controller (green rectangle).

54 | FIRST Tech Challenge PushBot Build Guide Part IV: Integrating the Op Modes and Electronics

Determining the drive wheel motor controller
This section shows how to determine which motor controller will be used to power the drive wheels and which will be used to power the arm motor. Both the Robot Controller and Driver Station need to be running for this section.

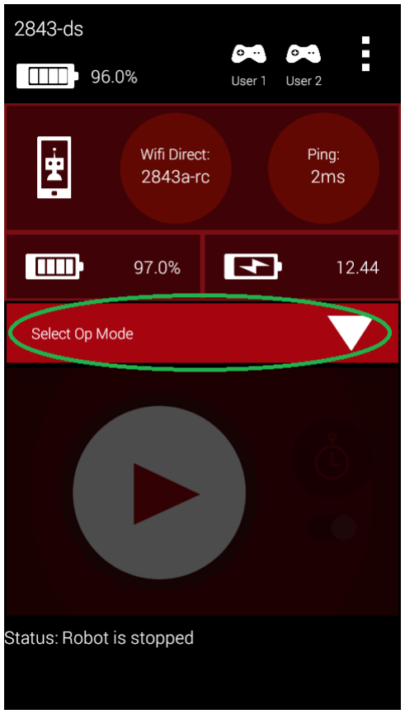
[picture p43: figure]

Step 1: On the Driver Station cell phone start the Driver Station app. Push the ‘Select Op Mode‘ button.

FIRST Tech Challenge PushBot Build Guide Part IV: Integrating the Op Modes and Electronics | 55
Step 2: The list of available Op modes are displayed. Select ‘PushBotManual’.

56 | FIRST Tech Challenge PushBot Build Guide Part IV: Integrating the Op Modes and Electronics
Step 3: Push the ‘Start’ button.
Step 4: Plug a DC motor into port 1 of a motor controller; it doesn’t matter which one. Hold the motor so it doesn’t roll while operating the joysticks. Push the left joystick of gamepad one up or down. If the motor moves, mark the motor controller as the drive motor controller (ex, tape with ‘Drive Controller’ written on it). If it doesn’t move, push the left joystick of gamepad two up or down. If the motor moves, mark the motor controller as the arm motor controller (ex, tape with ‘Arm Controller’ written on it).

FIRST Tech Challenge PushBot Build Guide Part IV: Integrating the Op Modes and Electronics | 57
Step 7: Notice that the telemetry data being sent from the Robot Controller app to the Driver Station app (lower portion of the display). On the Driver Station, press ‘Stop’.
Step 8: Turn the core power distribution module off.
Step 9: Exit the Driver Station and Robot Controller applications by using the over flow settings (the three dots in the top right corner).

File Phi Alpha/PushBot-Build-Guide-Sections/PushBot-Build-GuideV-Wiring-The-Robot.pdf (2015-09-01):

# FIRST® Tech Challenge

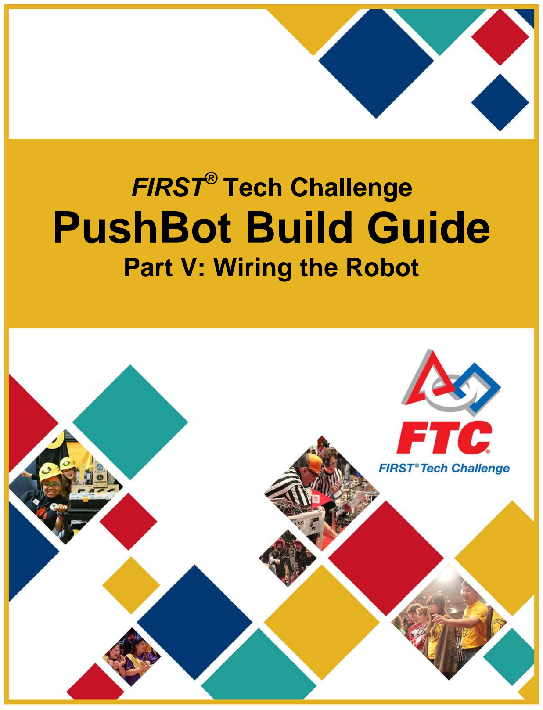
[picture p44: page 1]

# PushBot Build Guide

# Part V: Wiring the Robot

2 | FIRST Tech Challenge PushBot Build Guide Part V: Wiring the Robot

Revision History
Revision | Date | Description
1 | 8/15/2014 | Initial Release – by FTC Team #003 Australia, The Southport School
2 | 9/1/2014 | Replaced MATRIX with TETRIX content by former FTC Team #2843, Under the Son
3 | 8/6/2015 | Updated using the new kit of parts and new programming environment.

## Contents

## Wiring the Robot

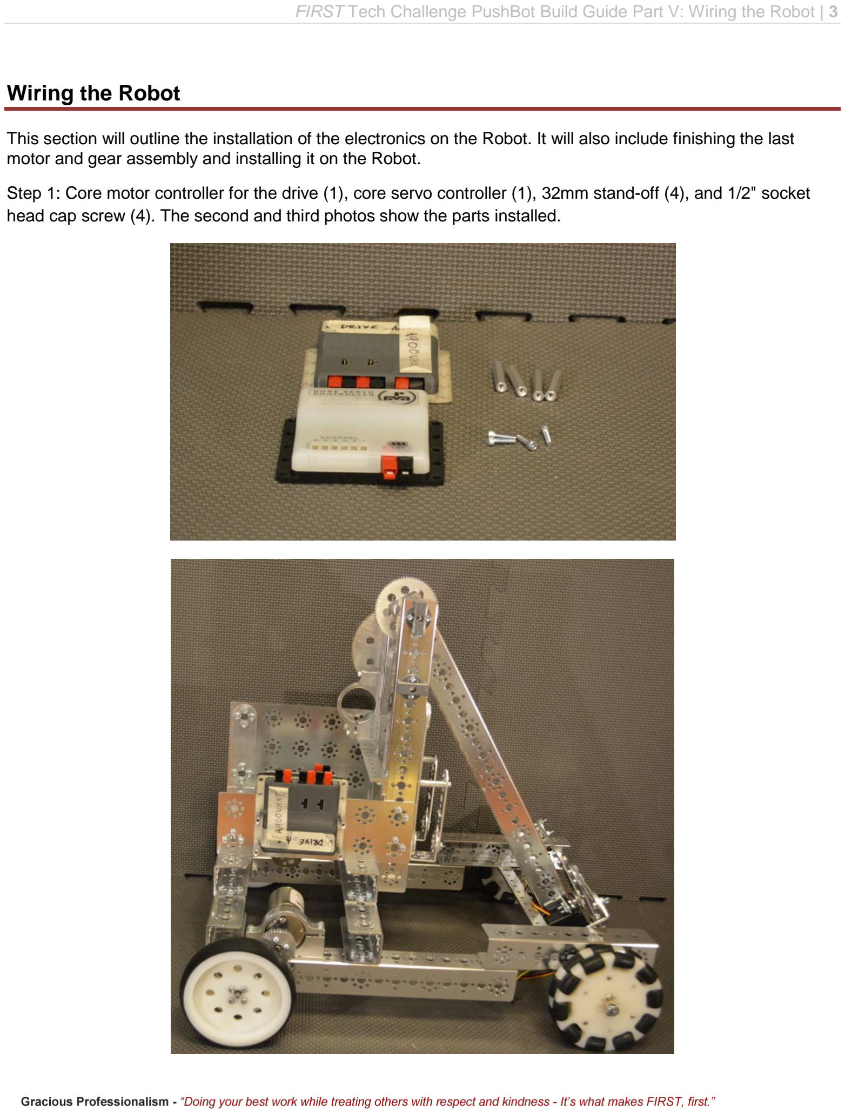
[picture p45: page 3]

FIRST Tech Challenge PushBot Build Guide Part V: Wiring the Robot | 3

This section will outline the installation of the electronics on the Robot. It will also include finishing the last motor and gear assembly and installing it on the Robot.
Step 1: Core motor controller for the drive (1), core servo controller (1), 32mm stand-off (4), and 1/2" socket head cap screw (4). The second and third photos show the parts installed.

4 | FIRST Tech Challenge PushBot Build Guide Part V: Wiring the Robot

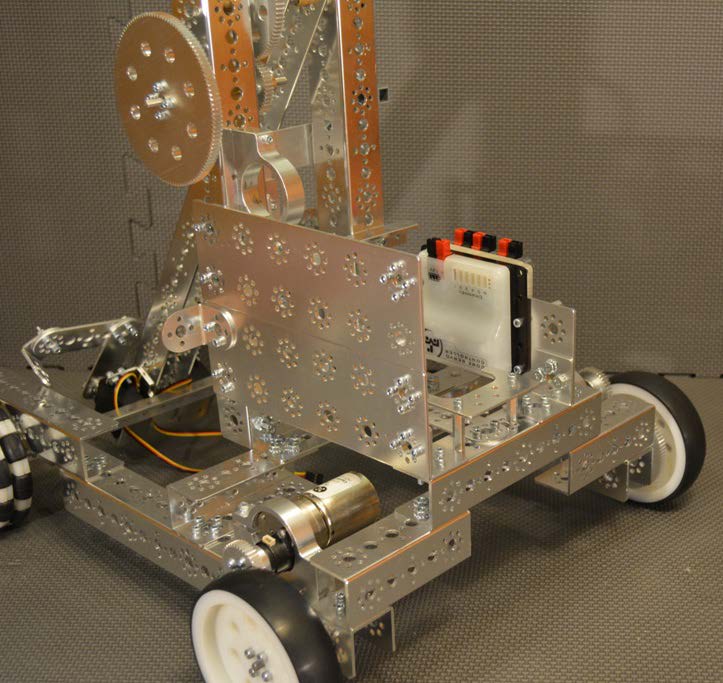
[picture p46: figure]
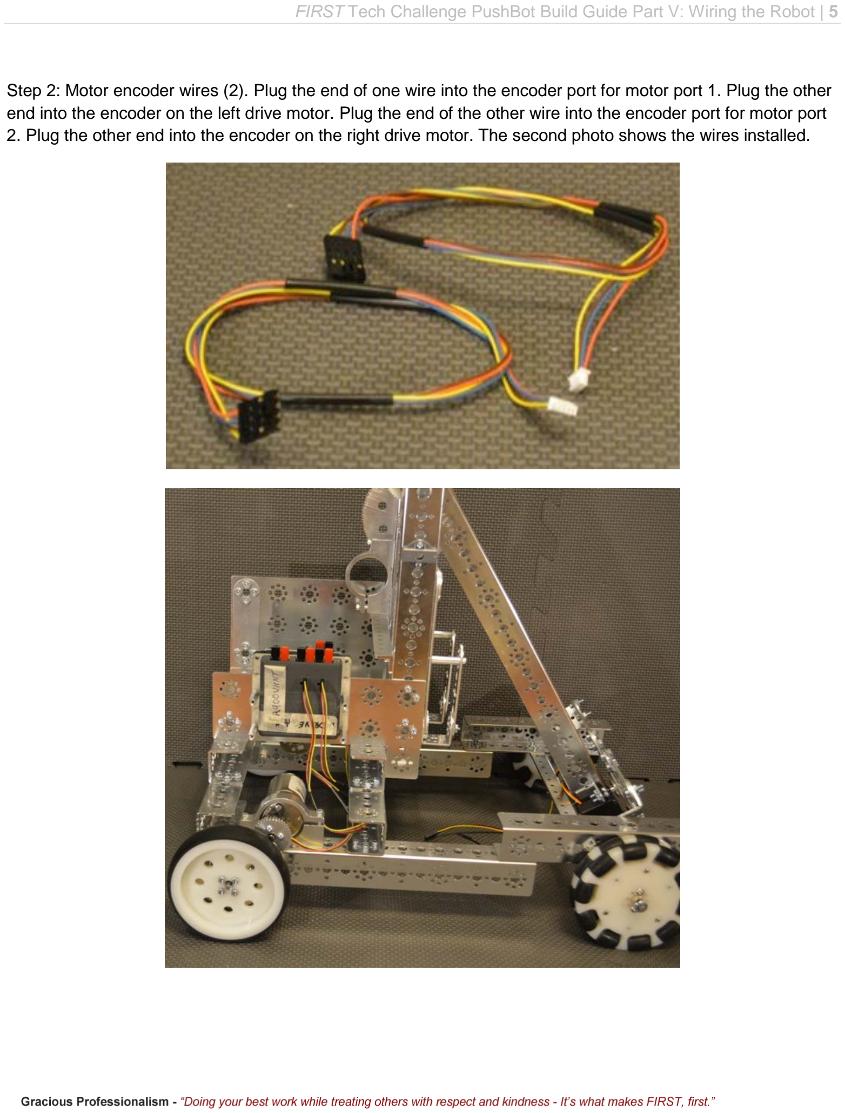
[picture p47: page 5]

FIRST Tech Challenge PushBot Build Guide Part V: Wiring the Robot | 5
Step 2: Motor encoder wires (2). Plug the end of one wire into the encoder port for motor port 1. Plug the other end into the encoder on the left drive motor. Plug the end of the other wire into the encoder port for motor port
2. Plug the other end into the encoder on the right drive motor. The second photo shows the wires installed.

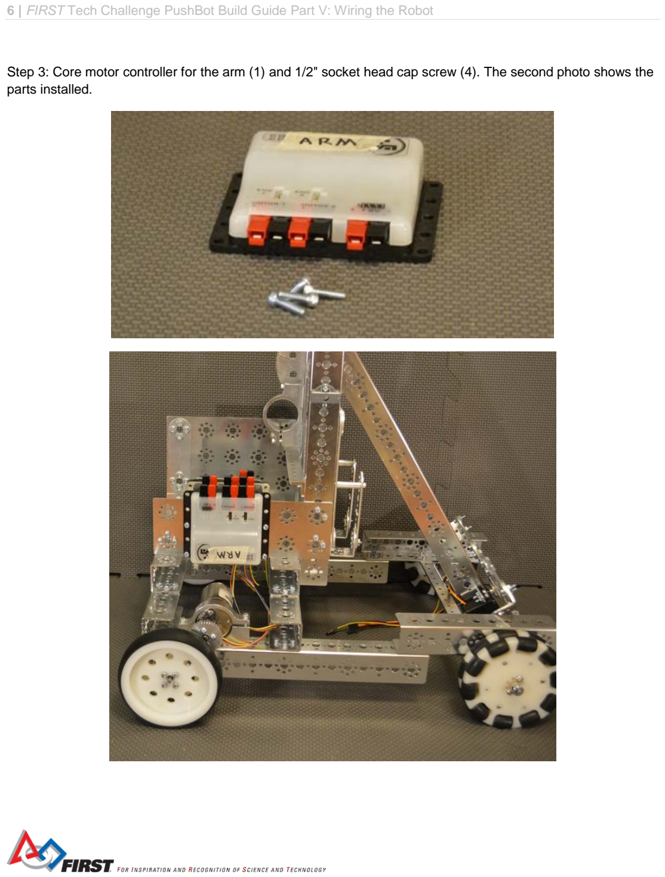
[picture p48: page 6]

6 | FIRST Tech Challenge PushBot Build Guide Part V: Wiring the Robot
Step 3: Core motor controller for the arm (1) and 1/2" socket head cap screw (4). The second photo shows the parts installed.


FIRST Tech Challenge PushBot Build Guide Part V: Wiring the Robot | 7
Step 4: Servo extension wire (2). Make sure that when you connect these to the servo wires that you match the colors. Also observe the orientation when installing in the core servo controller (black - b, red - r, yellow - w). The wires will be less likely to get damaged if they are run down the center of the arm channel and over the axel. The second photo shows the wires installed.


8 | FIRST Tech Challenge PushBot Build Guide Part V: Wiring the Robot
Step 5: Core power distribution module (1), 1/2" socket head cap screw (4), and keps nut (4). The second photo shows the parts installed.


FIRST Tech Challenge PushBot Build Guide Part V: Wiring the Robot | 9
Step 6: USB A male to mini-B USB cable (3). Connect one wire each between the core power distribution module and each of the two core motor controllers and the core servo controller. The second photo shows the cables installed.


10 | FIRST Tech Challenge PushBot Build Guide Part V: Wiring the Robot
Step 7: USB OTG cable (1), USB A male to mini-B USB cable (1). Connect the min-B end of the cable to the core power distribution module. Connect the other end to the USB OTG cable. Route the other end of the USB OTG cable to the right side of the phone holder assembly. The second photo shows the cables installed.

FIRST Tech Challenge PushBot Build Guide Part V: Wiring the Robot | 11
Step 8: Motor hub and gear assembly (1) (made in the Robot construction section, TETRIX DC gear motor (1). The second photo shows the parts assembled.


12 | FIRST Tech Challenge PushBot Build Guide Part V: Wiring the Robot
Step 9: Install the motor in the motor mount on the Robot tower. Rotate the motor in the mount to mesh the gears. Do not mesh the gear too tight or the motor will bind. Do not mesh the gears too loose or the teeth will slip.


FIRST Tech Challenge PushBot Build Guide Part V: Wiring the Robot | 13
Step 10: DC motor power wire (3). Connect the motor from the left drive to motor port 1 on the drive motor controller. Connect the motor from the right drive to motor port 2 on the drive motor controller. Connect the motor on the arm to motor port 1 on the arm motor controller. The second photo shows the wires installed.


14 | FIRST Tech Challenge PushBot Build Guide Part V: Wiring the Robot
Step 11: DC power wire (3). Connect one end of each DC power wire to any port on the core power distribution module. Connect the other end to the power input port on the core servo controller and the core motor controllers. The second photo shows the wire installed.


FIRST Tech Challenge PushBot Build Guide Part V: Wiring the Robot | 15
Step 12 TETRIX 12V battery (1). Install the batter between the battery clips and connect to the core power distribution module. The second photo shows the battery installed. It would be a good idea to use a zip tie or some other mechanism to hold the battery in place during competition.


16 | FIRST Tech Challenge PushBot Build Guide Part V: Wiring the Robot
Step 13: ZTE speed phone (1) configured as Robot controller. The second photo shows the phone installed (the arm is moved out of the way to show installation).

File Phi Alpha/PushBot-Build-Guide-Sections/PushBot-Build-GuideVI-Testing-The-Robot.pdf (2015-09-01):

# FIRST® Tech Challenge


# PushBot Build Guide

# Part VI: Testing the Robot

2 | FIRST Tech Challenge PushBot Build Guide Part VI: Testing the Robot

Revision History
Revision | Date | Description
1 | 8/15/2014 | Initial Release – by FTC Team #003 Australia, The Southport School
2 | 9/1/2014 | Replaced MATRIX with TETRIX content by former FTC Team #2843, Under the Son
3 | 8/6/2015 | Updated using the new kit of parts and new programming environment.

## Contents

FIRST Tech Challenge PushBot Build Guide Part VI: Testing the Robot | 3

## Testing the Robot

After the Robot is built, the programming is complete, and the electronics are installed, testing must be done to ensure everything came together as planned. This section assumes that the core power distribution module is powered on, the cell phones are powered on and the FTC apps are running.


Running an Op mode
Step 1: Operational Modes or Op Modes are program
modules that cause the Robot to perform specific
behaviors. The Robot Controller app should include some pre-installed op modes. If the Robot Controller has been successfully paired to the driver station, and if the Robot is running, then the Op mode buttons on the FTC Driver Station app should now be enabled.
Note that if the Driver Station app is connected successfully to the Robot Controller app, then some ping statistics should be visible at the top left hand corner of the Driver Station screen. In the image above the ping statistics reads “4 ms”. This means it took 4 milliseconds for the driver station to send a packet to the Robot controller and for the Robot controller to acknowledge the packet and send its acknowledgement back to the driver station.
The ping round trip time is a rough measure of network quality. As the round trip time increases, the network performance usually degrades. In our testing, an ideal round trip time is anything on the order of 10 milliseconds or lower. Sometimes the ping time period increases if there is a surge in network traffic or interference. If the period starts to increase to the order of or greater than 100 milliseconds, then there might be excessive network traffic or noise on the wireless channel that cell phones are using.
Step 2: Touch the Select Op Mode button to display a list of the available Op Modes sent to the Driver Station app from the Robot Controller app. Select “PushBotManual” from the list and the round play button should become brighter.

4 | FIRST Tech Challenge PushBot Build Guide Part VI: Testing the Robot


Note that any of the other Op modes will fail to work as the
names and number of controllers are different from the
PushBot.
Step 3: Once the PushBotManual Op mode is selected, the FTC Driver Station screen should change. The name of the selected Op mode should appear where the words “Select Op Mode” once was. Also, the Start button should be enabled.
If the Start button is pressed, then the Op mode will run indefinitely until the program terminates or until the Stop button is pressed. Press the start button and proceed to the next section.

FIRST Tech Challenge PushBot Build Guide Part VI: Testing the Robot | 5

Using the gamepads
This section describes how the two gamepad controls control the function of the Robot – make the Robot drive forward/backward, lift/lower the arm and open/close the hand.
The left joystick controls the ‘left’ drive motor and the right joystick controls the ‘right’ drive motor. The image above shows the back of the Robot.


Push both joysticks away from your body and the Robot drives forwards. Pull both joysticks toward your body and the Robot drives backwards. Push one joystick up and the other down and the Robot turns.

6 | FIRST Tech Challenge PushBot Build Guide Part VI: Testing the Robot

The programming sections show the programming necessary to use a second Logitech controller (F310) to raise and lower the arm and open and close the ‘hand’. This section describes how to use the controls on the gamepad to move the arm up and down and how to open and close the hand.
The ‘arm’ allows the Robot to lift items from the floor to at least 33” above the ground. The arm uses a 1:6 gear-ratio to enable the arm to lift moderately heavy items. Push the left joystick away from the body to raise the arm; toward the body to lower the arm.
The ‘hand’ is capable of opening and closing gradually. Button ‘X opens the hand; button ‘B’ closes the hand. The term gradually is used, because when the button is released, the servo stops at its last position – it doesn’t close or open all the way when the button is pressed.


FIRST Tech Challenge PushBot Build Guide Part VI: Testing the Robot | 7


Adjusting the Servos
If the servos don’t close all of way or they chatter, perform the following steps to correct them.
Step 1: Unplug one servo.
Step 2: Run servos to fully closed position using button X on gamepad 2.
Step 3: Remove the black screw from the servo. Remove the hand assembly. Replace the hand assembly such that the L bracket is as close to parallel to the arm as possible. Replace the black screw. See the pictures for an example. First picture is closed by software. Second picture is hand removed. Third picture is hand reattached in closed position.


8 | FIRST Tech Challenge PushBot Build Guide Part VI: Testing the Robot

Repeat step 1-3 for the other servo.
Final steps
- Now that testing has shown that all of the wires are connected properly, use zip ties or some other approved material to secure loose wires.
- It is recommended that an approved material such as non-skid be layered in the back of the phone holder to prevent damage to the phone.
- It is recommended that the phone be secured in the holder using a zip tie or some other mechanism to prevent it from being separated from the Robot during competition.
- Place non-skid around the gripper to provide extra grip…so hockey pucks, wiffle balls, pipes, racquetballs, crates, rings, blocks or practice golf balls, or red herrings can be collected with ease!

FIRST Tech Challenge PushBot Build Guide Part VI: Testing the Robot | 9

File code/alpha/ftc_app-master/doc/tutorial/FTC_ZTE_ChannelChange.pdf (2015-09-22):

DRAFT COPY: CONTENTS SUBJECT TO CHANGE

# FTC Training Manual

# ZTE Channel Changing App

FIRST Tech Challenge
8/3/2015


This document contains training material to introduce students and mentors to the next gen FIRST Tech Challenge robot controller platform.

DRAFT: Contents Subject to Change

FTC_ZTE_ChannelChange_v01.docx | Page 1 of 11

### Contents

### 1 Introduction

The FIRST Tech Challenge (FTC) has a new control system for its robot competitions. This new control system point-to-point system. This system has two main components, the Driver Station and the Robot Controller. The driver station communicates wirelessly with the robot controller.


Figure 1 - The new FTC platform is a point-to-point solution.

These two devices are paired together using a WiFi Direct connection. For this WiFi Direct connection, the Robot Controller device acts as the WiFi Direct Group Owner. If you are using a pair of ZTE Speed phones as your Driver Station and Robot Controller, then you can install a special app from the Google Play store that allows you to change the WiFi channel that is used by your Group Owner to establish the WiFi direct connection.


Figure 2 – You can use a special app to change the WiFi Direct channel for ZTE Speed

### 2 Downloading the App from Google Play

The channel changing app is available on Google Play for free for download. Note that this app should be installed on the Android device that is acting as your Robot Controller (i.e., the device that is acting as the WiFi Direct Group Owner). You do not need to install this app on your Driver Station Android device.

IMPORTANT NOTE: This WiFi Direct channel changing app will only work on the ZTE Speed phone. It will not work on other Android devices. It can only change the WiFi Direct channel for a ZTE Speed phone.

The ZTE Speed channel changing app is located on Google Play. To install the app, you first need to connect the ZTE phone to an available wireless network that has access to the Internet. Launch the Settings activity on your phone, and select the Wi-Fi item to display the Wi-Fi activity.


Figure 3 - Select your wireless network from the Wi-Fi activity.

Select your desired wireless network from the Wi-Fi activity and provide the password information required to access the wireless network.

Figure 4 - Launch the Google Play Store app.

Once you have connected successfully to your wireless network, launch the Google Play Store app from your phone. The Play Store app might prompt you to either login to an existing Google account or create a new one. Follow the onscreen instructions to either create a new (free) account or login to your existing account.

Once you have successfully logged in to Google Play, click on the search icon (a little magnifying glass) and search for the phrase “Wifi Direct Channel Changing”


Figure 5 - Search for the phrase "wifi direct channel changing"

Once you have found the WiFi Direct Channel Changing app, click on it and follow the onscreen instructions to install. Note that the application might prompt you to enter a credit card number or some other method of payment. The app is free and no payment method is required. You should be able to hit the “Skip” button to skip the process of providing a method of payment.


Figure 6 - Follow the on-screen instructions to install the app.

If you were able to install the app successfully, then there should be WifiChannelEditor icon on your Android device.


Figure 7 - After installing the app, you should see an icon on your Android's screen.

IMPORTANT NOTE: After you have successfully installed the app, go to your Wi-Fi settings menu and “forget” the wireless network that you used to connect to Google Play. In general, you do not want to be connected to any wireless networks with the exception of your FTC Driver Station device.

Figure 8 - Don't forget to forget the wireless network after the installation is complete!

### 3 Using the WiFi Direct Channel Changing App

### 3.1 Changing the Channel

After you have successfully installed the WiFi Direct channel changing app onto your Robot Controller ZTE Speed phone, you have two ways to launch it:

1. Click on the WifiChannelEditor icon to launch the app (see Figure 7).
2. You can also launch the app from the FTC Robot Controller app. Go to the Settings menu of the FTC Robot Controller app and select the Change Wifi Channel item to launch the channel changing app.


Figure 9 - Click on Change Wifi Channel from the Settings menu to launch the app.

To change the channel, use the drop down spinner control to select your desired channel.


Figure 10 - Use drop down spinner to select the desired channel.

Once you have selected your desired channel, press the Change button to force the Robot Controller device to change its channel.


Figure 11 - Press the Change button to force the channel change.

The app should display a notification indicating that the listening and operating channel for the WiFi group owner has been changed.

Figure 12 - The app should display a notification ("Reconfig Success!") once it has completed the channel change.
3.2 Un-Pairing then Re-Pairing the Driver Station to the Robot Controller.
Note that after you have changed the channel on your Robot Controller Android device, you might have to un-pair your Driver Station from the Robot Controller, and then re-pair the Driver Station back to the Robot Controller.

To un-pair the Driver Station from the Robot Controller, launch the Settings menu from the Driver Station app and select the Pair with Robot Controller item.


Figure 13 - Select Pair with Robot Controller.

From the Pair with Controller screen, select None to un-pair your phone.

Figure 14 - Select None to un-pair the device. Use the back arrow to return to the main screen.

Use the back arrow to return back to return to the main Driver Station screen. The screen should now indicate that the Driver Station is not paired with any WiFi Direct device.


Figure 15 - The Driver Station should now be un-paired from the Robot Controller.

To re-pair the two devices, launch the Settings menu from the Driver Station app again and select Pair with Robot Controller again (see Figure 13). Find the listing for your Robot Controller Android device (in this example “ZTE-026”) and select this item.

Figure 16 - Select your target device (in this example ZTE-026), then use the back arrow to return to the main screen.

Note that your Robot Controller Android device might prompt you to make sure you approve the connection request. On the Robot Controller device, click on the Accept button to approve the connection request.


Figure 17 - Click Accept to approve of the connection request.

Once you have accepted the connection request, the Driver Station screen should display that it has successfully connected to the Robot Controller.

Figure 18 - Once the connection request is accepted, the Driver Station should connect to the Robot Controller.

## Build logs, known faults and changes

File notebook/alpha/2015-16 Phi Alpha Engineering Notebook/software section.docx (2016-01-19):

Software

In the beginning, we met up with one of the seniors of the team that was the lead software. He was graduating and moving onto college. We met up with him and he helped us learn some java (basically the concepts), we had a few weeks before he left. We gathered up information from him as much as we could.

After he left we didn't really know what we were doing until we started watching and reading turtorials on the FIRST website. They explained it easier and it was easy to understand. After that we made some test programs for teleop to try it out, we tested a program for just servos and then tested a program for just motors. We got them to move! Then we did some autonomy test programs, it drove the robot in a square. Then we started on the competition teleop! We programmed six motors and two servos, We are trying to test out sensors. We made a simple autonomy to drive and park in the floor goal for the competition for now, but we are working on sensors such as the color sensor so that we can improve the autonomy.

Overtime we kept improving, there was some bumps in the road along the way but we got passed them! We kept learning and improving! I will get more into details in the next pages, let me show you what we have done this season and what we've learned!

This is one of the first programs we created to test out. We named it “SaladQueen” for fun. This program is to try out tank mode, which is where it uses both joysticks on one controller used for the drive. So when you use the left joystick it will move the left side of the robot and when you use the right joystick it will move the right side of the robot. When you push both of them forwards it will move both sides of the robot forwards. When you pull back both of the joysticks back it will move both sides of the robot backwards.

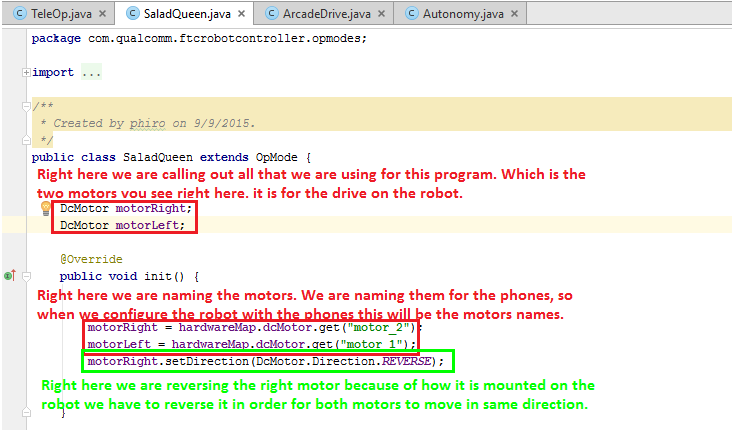
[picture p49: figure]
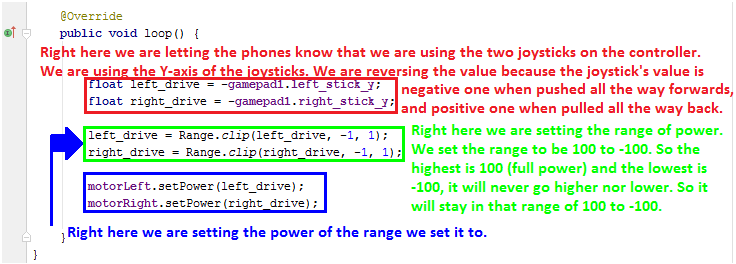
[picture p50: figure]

We named this program “ArcadeDrive”, in this program we are driving in arcade mode. We told you about tank mode, well arcade mode is different then tank mode. Let us explain arcade mode, arcade mode uses only ONE joystick, the left joystick controls the whole drive of the robot. It uses the X-axis and the Y-axis; the Y-axis is used for forwards and backwards, the X-axis is used for turning left and right. For competiton we use only use one controller so we use the arcade mode because we have more room to program other functions to the controller.

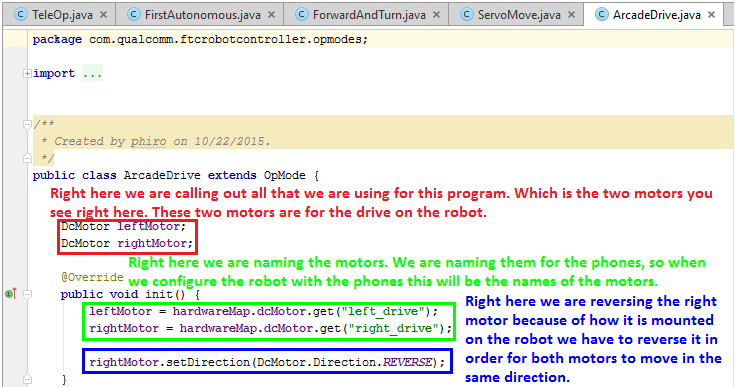
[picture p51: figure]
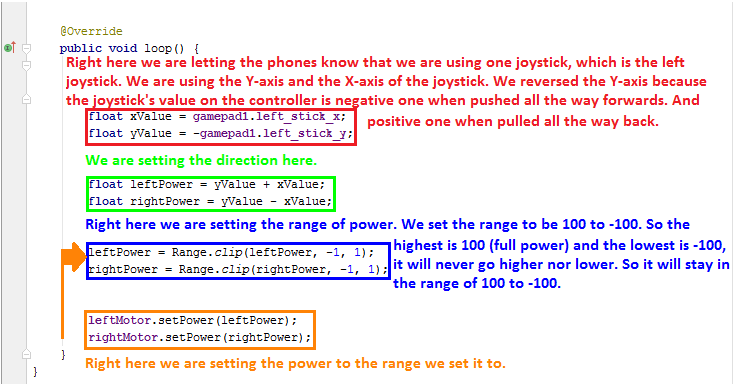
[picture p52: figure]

This is one of the test programs. In this program we were testing out two servos. We explained it better in the picture below.

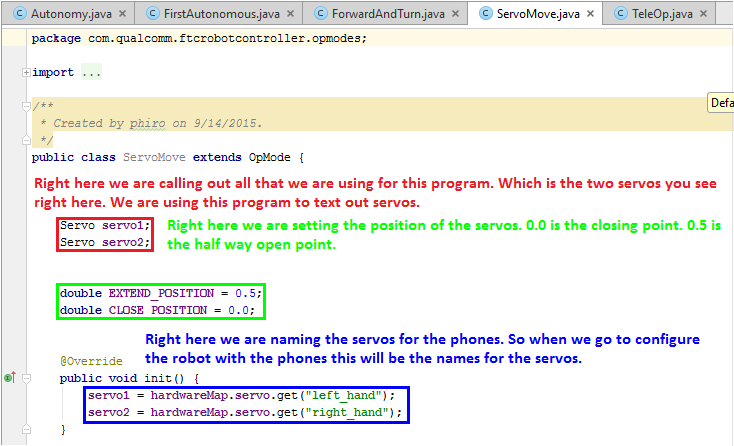
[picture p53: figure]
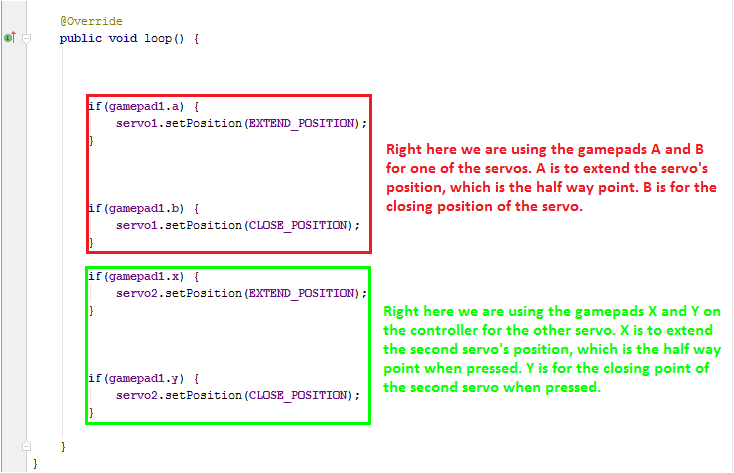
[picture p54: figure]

This was a test autonomy program, it is named “FirstAutonomous”. In this program we were only moving the robot forwards.

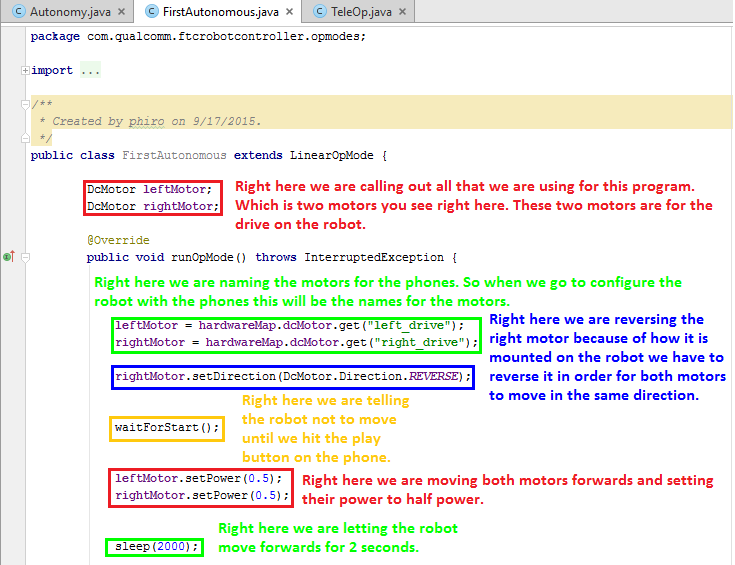
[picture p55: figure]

This is one of our competition autonomy, it is named “Autonomy”. This one is for when we are on the blue alliance. In this program we are moving the robot forwards and turning right, then we go forwards towards the floor goal and then we park on the floor goal. This is what we have for now but we are trying at the moment to improve and add more to this program to do more obstacles.

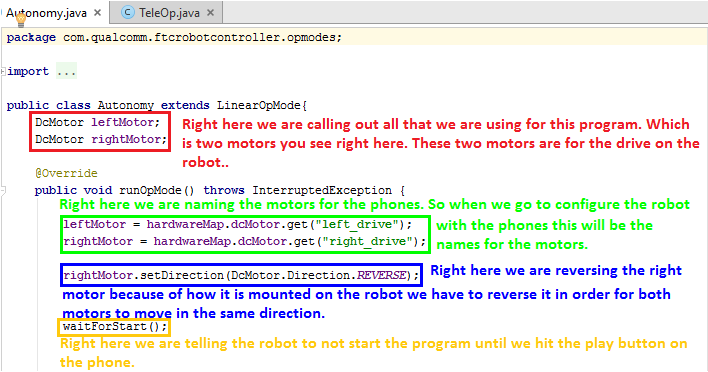
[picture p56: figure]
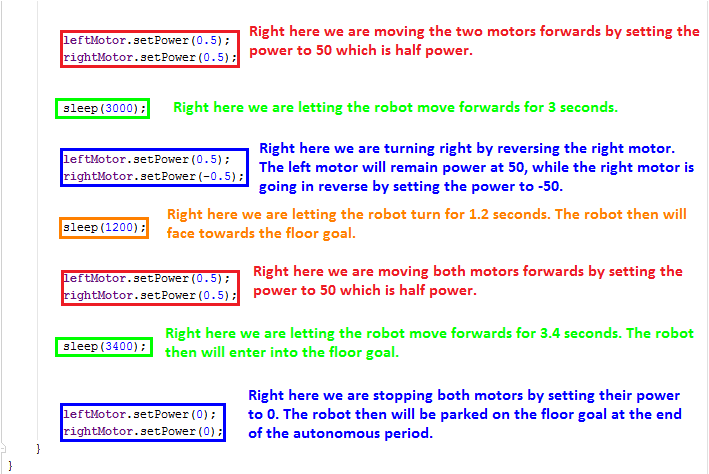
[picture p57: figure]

This is the other competition autonomy, it is named “Autonomy2”. This one is for when we are on the red alliance. In this program we are moving the robot forwards and turning left, then we go forwards towards the floor goal and then we park on the floor goal. This is what we have for now but we are trying at the moment to improve and add more to this program to do more obstacles.

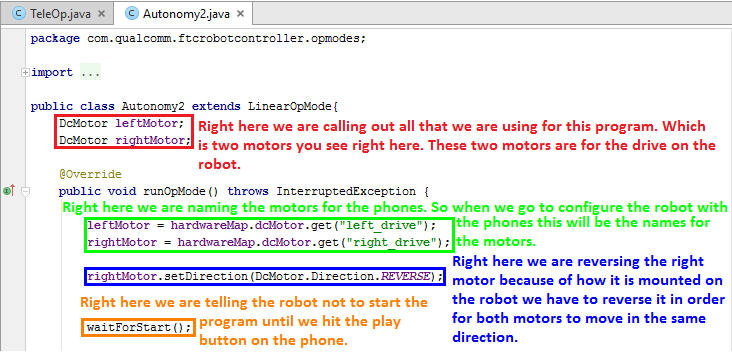
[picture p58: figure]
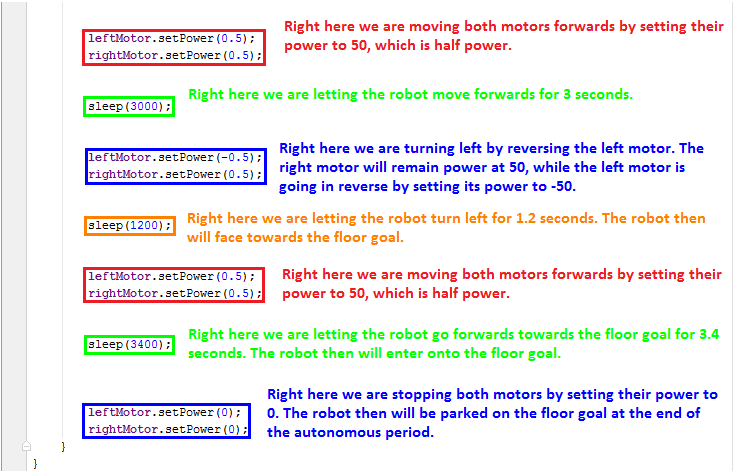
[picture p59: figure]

This is our competition TeleOp. It took us a lot of time and effort, there was a lot of bumps in the road but we got passed them and we accomplished a lot! We programmed six motors and two servos. We will explain more in details below!

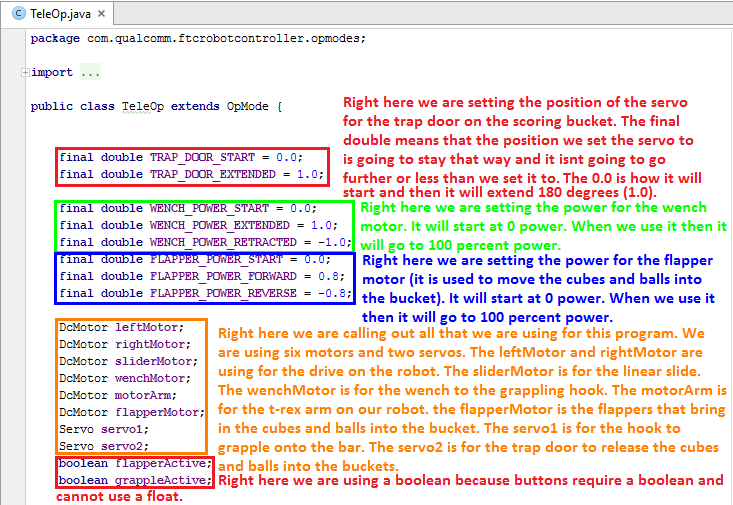
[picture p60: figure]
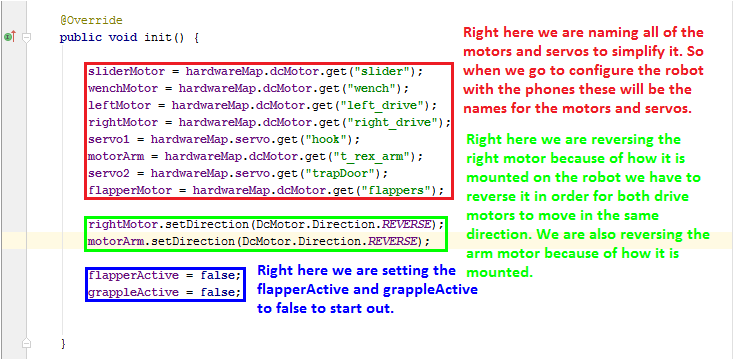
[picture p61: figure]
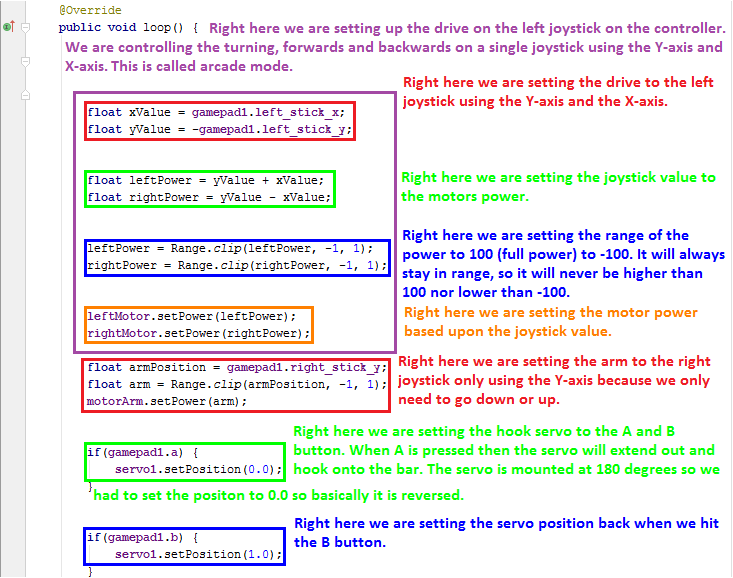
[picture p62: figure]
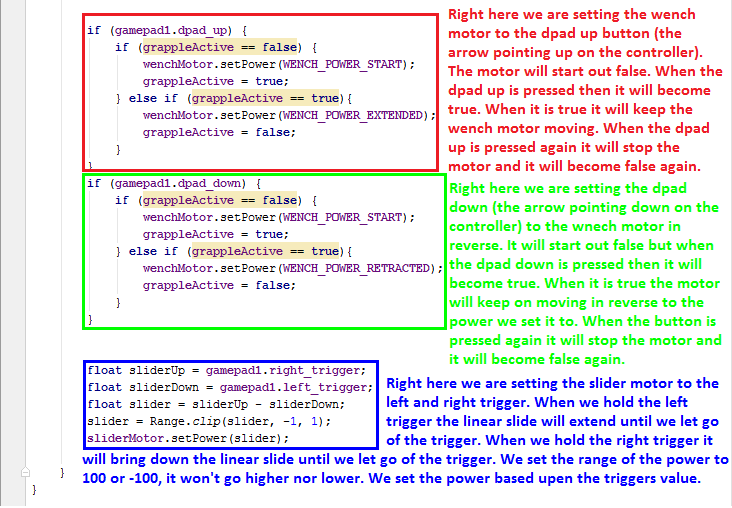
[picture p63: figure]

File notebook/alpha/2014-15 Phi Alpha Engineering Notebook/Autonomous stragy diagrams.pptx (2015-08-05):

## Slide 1

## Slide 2

After score we turn to the center goal.

We stop to raise the arm.

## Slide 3

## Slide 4

Robot turns to intercept.

We block the other team from scoring.

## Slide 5

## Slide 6

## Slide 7

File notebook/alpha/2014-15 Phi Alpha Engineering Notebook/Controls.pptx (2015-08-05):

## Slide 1

Ball Dunker

Reverse Conveyor

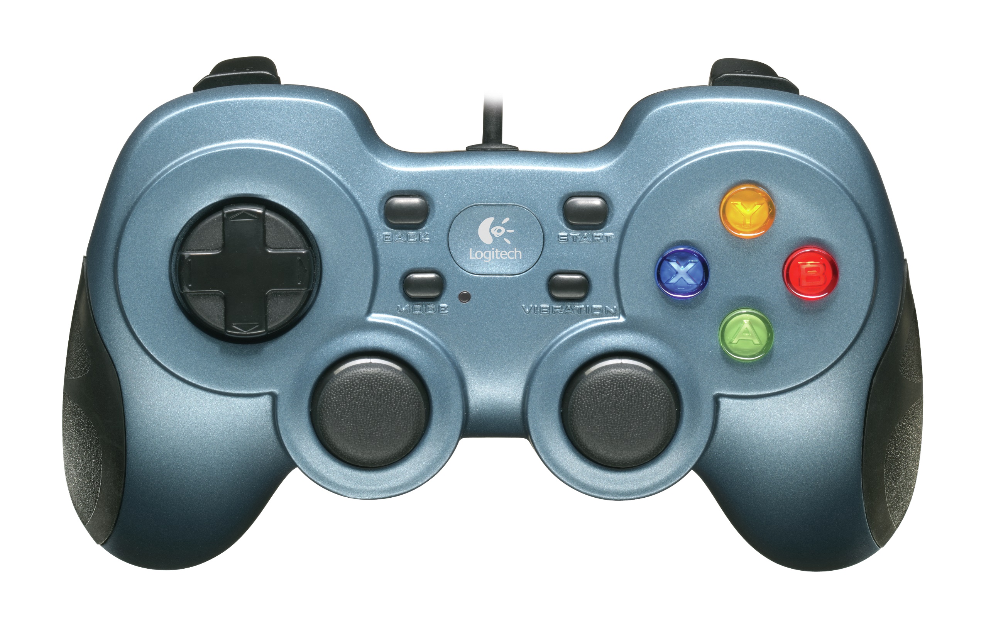
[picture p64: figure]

Tilt Bucket

Ball Release

Conveyor Belt

Drive

Arm Control

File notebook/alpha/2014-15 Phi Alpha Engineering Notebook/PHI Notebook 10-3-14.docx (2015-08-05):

NAME: Kaitlin Cox | YEARS ON TEAM: 3rd year on team

FAVORITE JOB ON TEAM: Driving the robot and working in the notebook, as well as learning to write basic software

HOBBIES: Creative writing- particularly medieval fantasy stories and fanfiction- art, computer programming and game design, and roleplaying

INTERESTING FACTS: Over the course of the 2013/2014 school year I wrote the rough draft for a novel that is more than 110,000 words in length. I am currently editing the manuscript. I am also attempting to make a computer game using the Construct 2 platform. I am a keraunomaniac, which means I have an abnormal obsession with lightning. Not everything I say is meant to be taken literally.

NAME: Becky Pierce | YEARS ON TEAM: 1st year on team

FAVORITE JOB ON TEAM: Hardware

HOBBIES: Playing volleyball and softball, running cross country and track

INTERESTING FACT(S): I’ve been homeschooled my whole life. I helped start an FLL team in 2011. I used to be on a bowling team.

NAME: Cierra Bachtelle | YEARS ON TEAM: 1st year on team.

FAVORITE JOB ON TEAM: Fundraising

HOBBIES: Volleyball, Football, Basketball, Babysitting, Walking, Swimming, Watching Movie, Baking.

INTERESTING FACT(S): I’m a really good babysitter, I love people, I love animals, I don’t know how to say the alphabet backwards, I’ve fallen and I couldn’t get up.

NAME: Joshua McMillan | YEARS ON TEAM: 4th year on team

FAVORITE JOB ON TEAM: Software

HOBBIES: Running, weight-lifting, biking, volleyball, tinkering with computers.

INTERESTING FACT(S): Paper originated from the papyrus in Egypt. Tomato is a fruit, not a vegetable.

NAME: Sergei Cox | YEARS ON TEAM: 1st year on team.

FAVORITE JOB ON TEAM: Hardware

HOBBIES: Baseball, building things, reading.

INTERESTING FACT(S): People call me different things and say my name wrong. I’m the weirdest person I know.

NAME: Hanna Creech | YEARS ON TEAM: 1st year on team

FAVORITE JOB ON TEAM: Hardware

HOBBIES: Photography, Baking, Piano (music), Swimming, And Drawing

INTERESTING FACT(S): I enjoy my pets especially my dog and guinea pig. I’ve been doing piano for over 6 years and the flute for 1. My favorite color is blue.

NAME: Cole Staron | YEARS ON TEAM: 2nd year on team

FAVORITE JOB ON TEAM: Driving/Notebook

HOBBIES: Martial Arts, Camping, Eating, Finding hobbies to write down

INTERESTING FACT(S): I can cook crapés, solve the Rubik’s cube, been to 30+ national parks, I’ve got a pet gecko, Noah’s bio is beneath mine!

NAME: Noah Killian | YEARS ON TEAM: 2nd year on team

FAVORITE JOB ON TEAM: Software

HOBBIES: Programming, Cubing, League of Legends, Electronics

INTERESTING FACT(S): I’m too lazy to procrastinate so I’ll procrastinate later. Cole’s bio is above mine!

NAME: Michael Kidman | YEARS ON TEAM: 3rd year on team

FAVORITE JOB ON TEAM: Hardware

HOBBIES: Golfing, riding my dirt bike and surfing/ stand up paddle boarding.

INTERESTING FACT(S): I do not like having duct tape put on my coat, ever!

NAME: Holly Creech | YEARS ON TEAM: 1st year on team

FAVORITE JOB ON TEAM: Working on the notebook, and learning hardware.

HOBBIES: Playing the piano, teaching the piano, and writing.

INTERESTING FACT(S): I love owls, chocolate, listening to music, and spending time with friends.

NAME: Eddie Pierce | YEARS ON TEAM: 3rd year on team

FAVORITE JOB ON TEAM: Hardware design, LabView programming

HOBBIES: Playing clarinet, PC gaming, novel writing, sketching, airsofting

INTERESTING FACT(S): I have been known on the team as the designated target for all robots. For my first year on the team, I was called the Dementor, but that has since changed to Bones.

NAME: Kayla Bachtelle | YEARS ON TEAM: 1st year on team

FAVORITE JOB ON TEAM:

HOBBIES:

INTERESTING FACT(S):

NAME: Luke McMillan | YEARS ON TEAM: lst year on team

FAVORITE JOB ON TEAM:

HOBBIES:

INTERESTING FACT(S):

NAME: Joseph DeVore | YEARS ON TEAM: 1st year on team

FAVORITE JOB ON TEAM:

HOBBIES:

INTERESTING FACT(S):

NAME: Scott Kidman | YEARS ON TEAM: 1st year on team

FAVORITE JOB ON TEAM: Hardware design.

HOBBIES: Golfing, Dirt bikes, Tent camping.

INTERESTING FACT(S):I have a Yamaha TTR130 Dirt bike.

NAME: Anna Leland | YEARS ON TEAM: 1st year on team

FAVORITE JOB ON TEAM:

HOBBIES:

INTERESTING FACT(S):

NAME: Jonathan Lokos | YEARS ON TEAM: 4th year on team

FAVORITE JOB ON TEAM:

HOBBIES:

INTERESTING FACT(S):

SAMPLE MEETING LOG- MM/DD/YYYY

HARDWARE

Author initials

SOFTWARE

Author initials

NOTEBOOK AND/OR OUTREACH

Author initials

ATTENDENCE

MEETING LOG- 9/8/2014

HARDWARE

Author initials

SOFTWARE

NK

Our goals for tonight were to give some of the freshmen an intro to programming in RobotC which is the language our team uses.

Tonight we explained the basics of RobotC to the freshmen interested in learning it. We explained pragmas, includes, and basic motor controls.

ATTENDENCE- Cierra, Kayla, Kaitlin, Hanna, Holly, Joseph, Mike, Noah, Anna, Jonathan, Josh, Luke, Cole

MEETING LOG- 9/11/2014

HARDWARE

JL

Our goals for tonight where to rebuild both of our 2013-2014 chassis so we could mount prototypes and test them. We also wanted to brainstorm further ideas for ground intake systems.

Tonight we accomplished rebuilding and wiring both robots. We succeeded at mounting some prototypes on one of the robots and the freshmen learned how to program the other. We familiarized some of the freshmen with parts of the TETRIX kit. We also brainstormed an inverted funnel for scoring balls in the tubes.

SOFTWARE

JM

We further instructed freshmen on programming, teaching them about pragmas, how to control the motors, and how to create autonomies. We also explained basic C syntax.

NOTEBOOK

KC

Tonight we set up a syncing application to allow us to sync important files such as the Engineering Notebook, code files, and pictures between computers. We also set up a new, more detailed format for the meeting log.

ATTENDENCE- Cierra, Kayla, Kaitlin, Hanna, Holly, Mike, Noah, Anna, Jonathan, Josh, Luke, Becky, Eddie, Scott, Sergei

MEETING LOG- 9/15/2014

HARDWARE

Author initials

SOFTWARE

Author initials

ATTENDENCE-

MEETING LOG- 9/18/2014

HARDWARE

SC

We wanted to finish our prototypes, make more prototypes, and build our game field.

The main prototype that we have been working on is a conveyor belt that picks up balls and carries it up into a bucket. The bucket is mounted on a linear slide that carries it with the balls to the height of rolling goals. We also made a smaller tube that is around the conveyor belt to help both ball sizes go up through it into a bucket and extended the width of the flaps of card board so that the conveyor belt could pick up both sizes of balls, and made a bucket to hold the balls to score them into the goals. In addition to this, we prototyped some ideas for grabbing the rolling goals.

SOFTWARE

JM

We discussed finding distance from acceleration and finding distance from IR sensor values. We were theorizing ways to use double integration so that we would be able to ascertain accurate distances from the accelerometer and are now trying to find equations that will allow us to do so. Unfortunately, double integration can greatly multiply error so we need to find a way to make measurements as accurate as possible. We are also theorizing ways we can find distance with Ir finding the angles we are from the IR emitter and then using trigonometry to find our relative position.

ATTENDENCE-

MEETING LOG- 9/22/2014

HARDWARE

CS

Tonight we finished off the field build by assembling the last parts of the ramp, and adding the tapped lines to the floor to mark off the specified zones/goals.

Our first prototype was a small “L” shaped piece designed with a bendable edge that would fit on the back of the robot. The robot would drive backwards bending the edge to snap onto the rolling goals, and then proceed to drive to the scoring zone. This piece could also be modified with a servo to allow it to be raised/lowered onto the rolling goal lip.

Our next prototype we fitted onto a square-bot to get a better look at it. It consisted of a conveyor belt fitted to raise the whiffle balls into a holding container. Once the container was filled, an arm would proceed to raise the container, and dump the balls into whatever rolling goal was desired.

Our third prototype for the nigh still needs some work. It is designed to be a tube that will pull in the whiffle balls using foam prongs attached to motors. A sensor will count the amount pulled in, and will stop the mechanism at the desired amount. After this, the robot will be driven up to a rolling goal, and the balls will be deposited out of a “U” shaped piece at the top of the container. In order for this design to work, we still need NASA to cut out certain sections of the tube, and supply additional parts.

Our final design for the night consisted of an arm, holding area, and an elevator. We designed an arm to catch balls, and put them into a sloped holding container. The balls would all roll to the corner where an oval shaped conveyor would scoop the balls out, flip over, and dump them into a desired container on their “O” shaped path.

SOFTWARE

Author initials

ATTENDENCE-

MEETING LOG- 9/25/2014

HARDWARE

CPB

Some of the things we did tonight, we built some prototypes. One of the prototypes we built was a little box hand that helps us pick up balls. It’s workable and easy for someone to operate. Another prototype that we did was, attach a second linear slide for extra height. Finished wiring the bot. Finished building the shield around the conveyor belt, to contain the balls when we pick them up. Create a funnel to help guide the balls into conveyor belt.

SOFTWARE

JM

We have coded our first algorithm to find distance with Acceleration by using kinematic equations. Unfortunately, we are having issues printing the output. We hope to fix this issue shortly. We are debating if relative position from IR values is feasible or not.

ATTENDENCE-

MEETING LOG- 9/29/2014

HARDWARE

Author initials

SOFTWARE

Author initials

NOTEBOOK AND/OR OUTREACH

Author initials

ATTENDENCE

MEETING LOG- 10/3/2014

HARDWARE

Author initials

SOFTWARE

Author initials

NOTEBOOK AND/OR OUTREACH

Author initials

ATTENDENCE

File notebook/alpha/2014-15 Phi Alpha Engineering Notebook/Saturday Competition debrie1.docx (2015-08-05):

Saturday Competition debrief

Good things:

- Ball collecting mechanism
- Hardware reliability
- Arriving at the competition with a robot
  - Good prototype robot
- Facing challenges
  - Hardware
  - Software
- Got to the semi-final round
- NXT issue solved

Bad things:

- Notebook?
- Linear slid
  - Speed
  - Stability
- Competing for the awards
- Connection issues
  - Connecting with the playing field(Samantha module)
  - Losing connection during the game
- Bad wires
- Appearance of our bot

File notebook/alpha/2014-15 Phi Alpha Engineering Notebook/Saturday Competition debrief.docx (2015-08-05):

Things to work on

- Everyone
  - Packing list
  - Knowing what’s on the robot
  - Consent forms online
  - Sponsor form
  - A very messy table
  - Team brochure
  - The control award
  - Another NXT
  - Having a group of people build a mock chassis or practice box
  - Winning awards
    - Look at the requirements
    - Meet them
  - Understanding our budget
  - Be prepared to answer on-the-spot questions
  - Brainstorm judging questions
  - Team pictures
- Notebook
  - B.O.M., budget, etc.
  - The Bill of materials SEPARATE FROM THE NOTEBOOK
- Software
  - WIRING DIAGRAM!!!!!!!!!!!!(In the team brochure)
  - IR sensor
- Hardware adjustments
  - Two linear slides
  - Pulling our bucket down
  - The rolling goals and keeping them with you
  - New bucket
  - Adjust the tread
  - Appearance of our bot
  - Being prepared for Hardware and software inspections
  - Scoring in the center goal
  - New winch
  - Spare motors
  - Overall attention to detail
    - Don’t be content with something just “working”
    - Be content when it’s awesome
  - Drawings before prototypes
  - On/off switch accessibility
  - Increased penalties on tube touching
- Miscellaneous
  - Don’t try to do everything
  - The team needs to be in control of THEIR robot

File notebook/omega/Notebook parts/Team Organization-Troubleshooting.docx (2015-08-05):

TEAM ORGANIZATION:

PHI Omega and PHI Alpha:

PHI Robotics actually isn’t registered as one team- it’s registered as two. However, even though PHI Omega and PHI Alpha compete as separate teams, build two different robots, and consist of different team members, they come together to form the organization PHI Robotics. Although the teams often seem very different, PHI as a whole operates more as one team than two. Members of both teams share ideas, prototypes, and help each other whenever help is needed.

PHI Alpha and PHI Omega also share funds and parts. They fundraise together, and also joint-hosted the 2014 High Desert Qualifying Tournament. All in all, even though the teams can look very different from the outside, they really come together to make up a larger team- PHI Robotics.

In the beginning of the year, PHI Robotics begins as one team, but as prototypes are developed and integrated onto basic chassis, the teams begin to form naturally. After a few months of working with this, PHI has usually divided naturally into PHI Alpha and PHI Omega. These teams don’t always change much from year to year, however, with the exception of new members joining the team and senior members’ graduation. Jonathan, Jacob, Mike, Eddie, and Kaitlin were all members of PHI Omega during the 2012-2013 season and some of the older members were even part of Omega the previous year.

PHI Omega’s Organization:

PHI Omega also has its own team structure. As the most senior member, Jonathan leads the team over all, as well as taking leadership in the hardware area. This year he is mentoring three new members- Anna, Hanna, and Sergei- in hardware. Eddie also helps with hardware, though he is also a member of the software team.

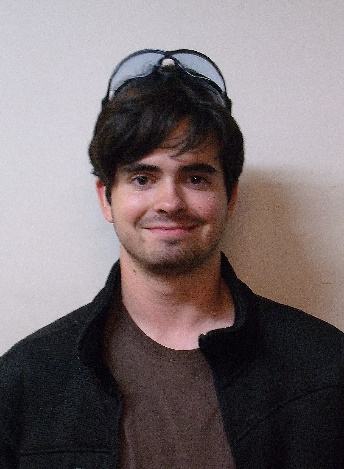
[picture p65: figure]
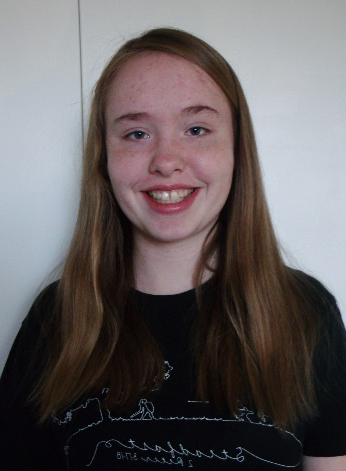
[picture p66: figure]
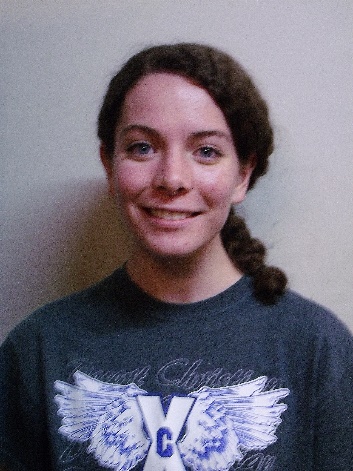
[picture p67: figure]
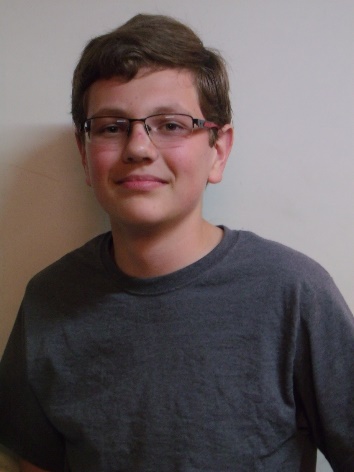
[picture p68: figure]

The hardware team

Noah, Eddie, and Becky make up the software team and are responsible for programming the robot. Noah is the software captain and does much of the major programming, and Becky is learning software from him and Eddie.

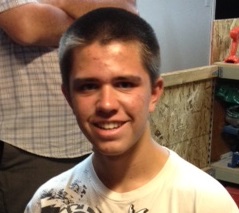
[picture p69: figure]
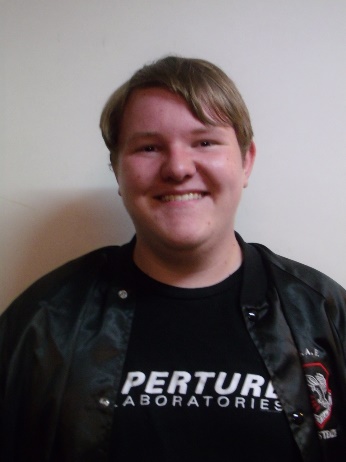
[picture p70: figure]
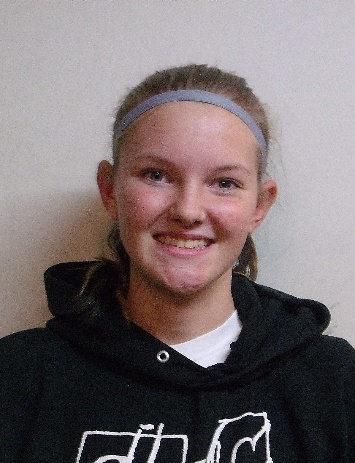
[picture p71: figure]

The software team

Kaitlin and Holly coordinate the Engineering Notebook. However, even though they coordinate the notebook, the rest of the team works primarily on their respective sections- the hardware team handles the hardware section, the software team the software section, and so on. All members work on the meeting log, as well as adding to the outreach section and other general sections.

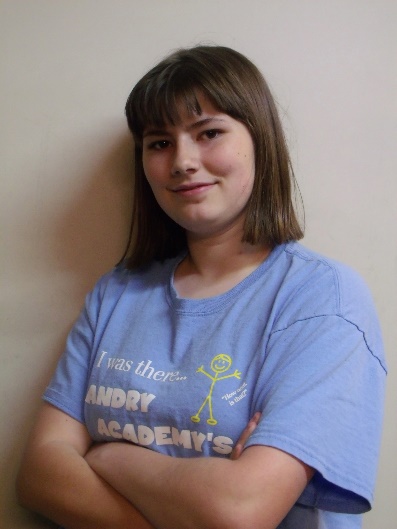
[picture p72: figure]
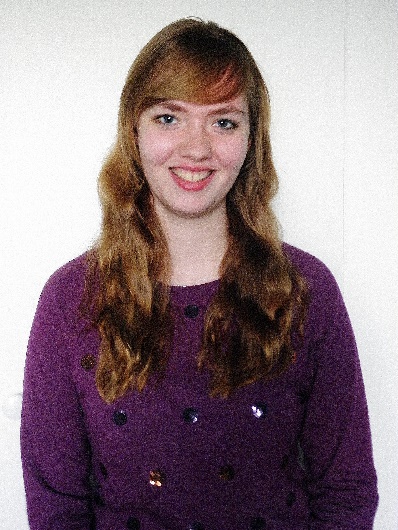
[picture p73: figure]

The notebook team

The Mentors:

Of course, no team would be complete without their mentors. Although PHI works primarily on its own, its mentors offer feedback on their designs, keep the teams focused, and help them plan and manage their time wisely. By helping us learn these skills, they help prepare us for life.

The Stinsons have been running PHI for seven years as an FTC team, and for even longer since PHI was first a VEX robotics team. Over the years they have generously opened up their house to us, first allowing PHI to work in an upper room and then, as the team expanded, giving the team their entire garage. Even after Dylan graduated from robotics, they continue to host the team and keep it running. They also have given much time and effort to helping prepare for the High Desert Qualifying Tournament in the two years it has run (2013 and 2014). PHI is greatly blessed to have such amazing mentors.

Dylan himself is a graduated PHI mentor and a computer genious. It has been said that all Dylan has to do is walk into a room and immediately all the electronics begin to work. At the High Desert Qualifying Tournament which PHI hosted, Dylan kept the software running as smoothly as possible. Now he helps guide our software team in the right direction when they get stuck on a tough coding problem. When he’s not offering advice on software or doing college work, Dylan designs drills to help keep the team in peak driving condition.

Mr. Pierce and Mr. Cox are new mentors to PHI as of the 2014-2015 season. But although this is their first year mentoring, both have experience with PHI from their childrens’ time on the team.

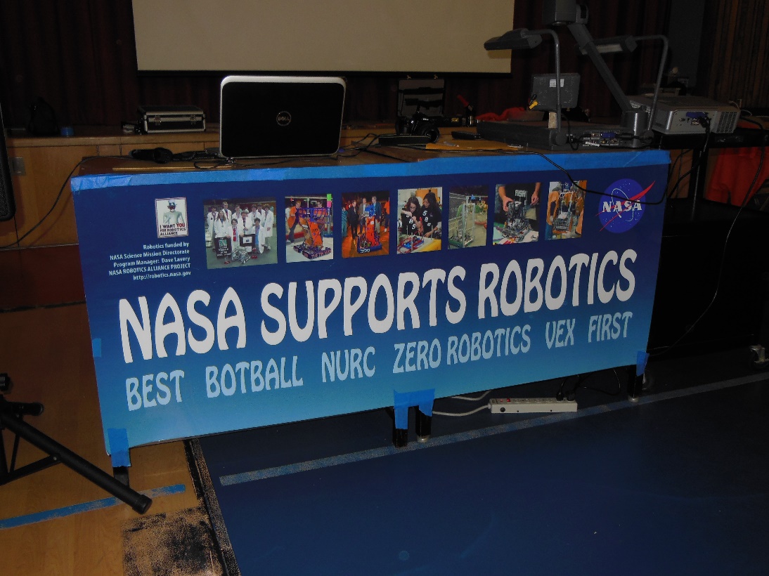
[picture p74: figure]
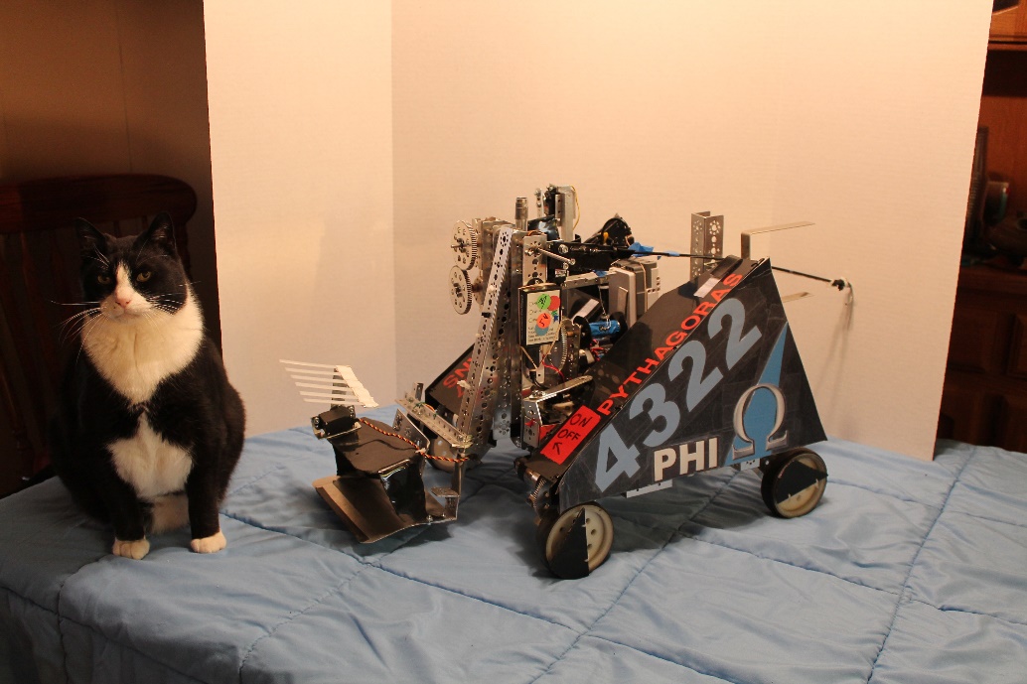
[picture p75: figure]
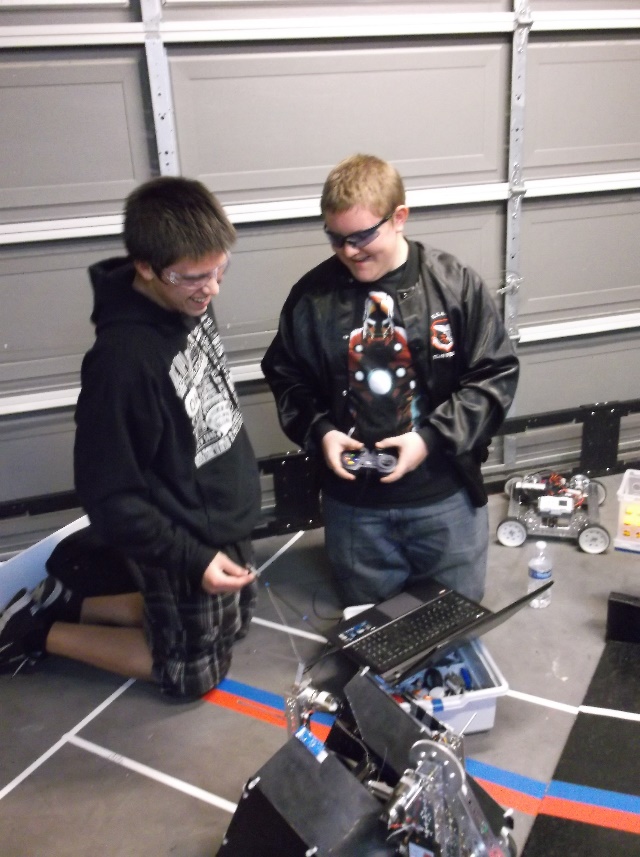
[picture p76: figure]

Promote Award Video Entry:

# PROMOTE VIDEO

This year Phi Robotics decided to make an entry for the Promote Award. Both Phi Alpha and Phi Omega collaborated to make a video submission for the award. The teams came together and submitted their answers to this year’s challenge- Why I Chose FIRST. Then we compiled those answers and combined them into a 60-second video.

We wrote several drafts of the script we used for the video. The final draft is included below:

Person A - Why First?

Person B - Why First?

Person C - Why First?

Person D - Why First?

-Screen shows a collage of "Why First?"

- Screen shows a large "WHY FIRST?"

Luke - I chose FIRST because it's a way to learn new things ()

Kaitlin - to challenge ourselves ()

Hanna - to give us head starts to our futures ()

Mike - I chose FIRST because it builds teamwork and cooperation ()

Person B – It brings together new friends (Cole)

Person C – It provides a way to interact with others who share our interests (Sergei)

Person A -I chose FIRST because it teaches responsibility (Becky)

Person B – It teaches us to act independently and take initiative (Holly)

Person C – how to become both good leaders and good followers (Jonathan)

Person D – to learn to sacrifice for the good of others (Eddie)

Person E – to learn diligence, confidence, and determination (Holly)

Person F – and to become more creative (Cici)

Person A - I chose FIRST because it's a way to share gracious professionalism (Mike)

Person B - to encourage others (Scott)

Person C - to help others (Becky)

Person A - I chose FIRST because it's a way for us to reach out to the community (Kaitlin)

Person B - to participate in and host events (Kayla)

Person C - to partake in healthy competition (Hanna)

All- I chose FIRST because it’s a way to have fun!

*credits*

# TROUBLESHOOTING

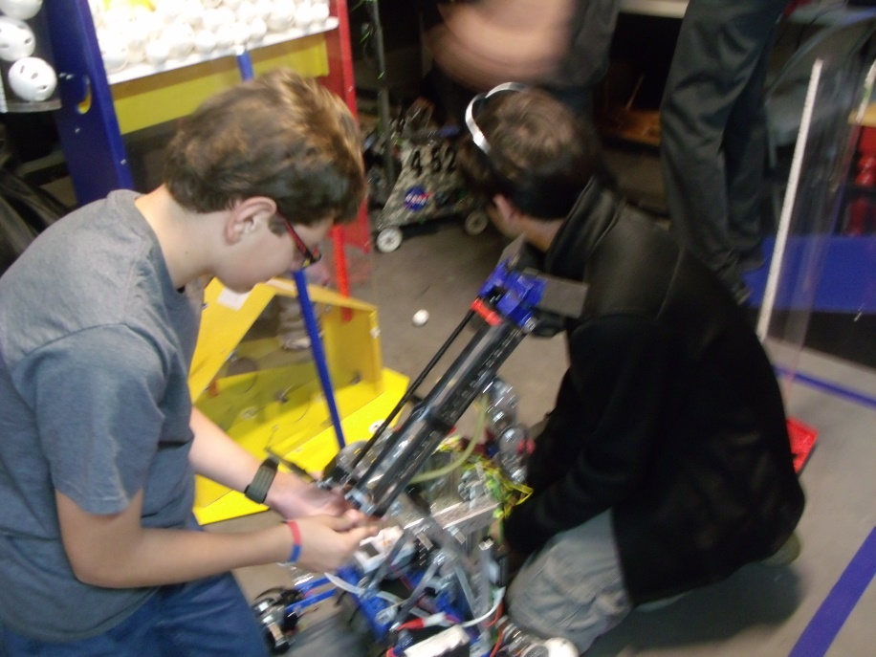
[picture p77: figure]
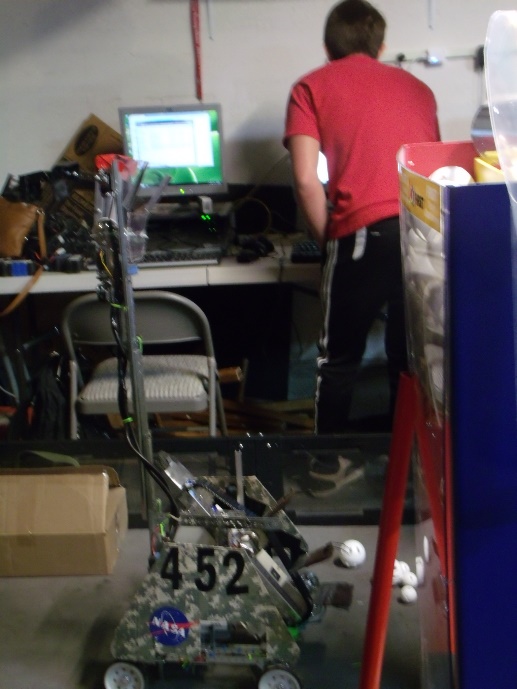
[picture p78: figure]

TROUBLESHOOTING

Here are some of the main troubles that we faced this year and the solutions that came about. Here we also have some of our main robot designs and how the changes came about over time. This also shows our process in learning how to develop a mindset that doesn’t let you give up until you know that you tried everything.

Can you handle the shock?

We decided to make a robot chassis that has shock absorbers. In order to do this we needed to make our own parts. We ordered the parts to be metal shopped from NASA we also designed some plastic pieces that NASA also printed. One piece is a rectangular channel that the motor is attached to. Another one is a little square piece that holds the supports that hold the two halves of the robot together. When we put the robot together we used some surgical rubber tubing to make the shocks.

As we put more on the robot it got heavier and heavier it got so heavy that the shocks collapsed. We ended up putting more surgical rubber tubing on it to give it more spring so that it could hold its load up.

After we made the chassis we drove the robot off the ramp to test the shocks. One of the times we drove it off the ramp the plastic printed part that the motors are attached to sheered in half. This occurred because the plastic was weaker than the metal that we usually use. So we modified the piece and made it thicker so that it could take more.

Later when we were driving the robot around the chain kept coming off the gears. We looked at the bottom we found that the screws were eating their way through the plastic. We sent in more requests to have more be made and to put metal on them to keep the screws in. We also made a temporary fix by putting washers under the screws.

When we were wiring we put the robot down wrong and one of the pieces that hold the two halves of the robot together broke in half. Because of this, one part of the robot started dangling. We found another of those pieces and put it on. We also sent in the request to make more and to have those metal shopped.

Rise of Khan I


Our first design was a threefold arm that went up with a tube that on top called the Da Vinci tube. The threefold arm had two metal pieces or the tube and a metal piece that is parallel to the other metal c channel.

The first problem was that the holes that we drilled in the metal pieces were not lined up right so the chain that we needed to make the arm go up and to keep the arms parallel was too long and if we shortened the chain it was too short. So we drilled more holes in the bar and the chain fit a little better but no perfectly so we used zip ties to attach the chain together in the center. The zip ties still allowed the chain to move but it also tightens it.

Another problem we had was that we could not get the arm to fit into dimensions because we had one arm on each side and we needed to put a motor on each side but when we did this the motor would stick out. Because of the design we needed worm gears to keep the arm in its proper position without them the arm would just slip back and not stay up but we did not have enough room because the tube took up too much space. We spent hours on the arm and found that we could not push it into dimensions. We then decided that it was not worth the time to make the arm work and decided to work on another idea.

Collapse of Khan II

Our next idea was a robot that had two linear slides and the Da Vinci tube between them. The tube would use a conveyor belt that we made to bring balls up and to score them. The problem with the bot was that we couldn’t make a good enough belt for it that would actually bring the balls to the top.

Before we had the belt we made some spinning blades out of Styrofoam. The blades would jam the balls in the tube.so we went to our first belt was made from Styrofoam and we could not get the belt to move. We then put grip cloth on the bottom of it to help it grip the axel that was supposed to move it. But even with the cloth there still was too much friction to overcome and the belt would not spin.

Our second belt was made from chain we took some of the pins out of the chain and replaced them with small nails. Then we put some paddles on the nails by taping some Styrofoam to them. The problem with that was that the chain was too loose because the nails gave it more give than the pins that were there originally did.

Eventually we gave up on using a belt or chain to move the balls up because. So instead we had the whole tube just rotate up so that the balls would just roll out into the tube. The linear slides that moved the tube up had way too much weight on them because of the whole scoring mechanism on top. So we needed to put another motor on the lift to make it go up. Even with another motor the motors would skip gears and strain to get up. We decided to not go along with this idea because it took a long time to get it working and it also took a long time to make it work and the whole thing was just too heavy and complicated.

Our wiring misadventure

In the last one of the meetings we found a problem with our robot. The problem was that as you drove the robot forward and then suddenly changed direction the whole robot would stop working. Also the battery would drain very quickly and we burned out a fuse. First we thought that it was a programing problem, so we tried a different program. But it still did the same thing so we flipped the robot over and did some more tests. We did enough tests so that we could predict when the robot would die.

We decided to change out the wires that connected to the robot and connected them to a different motor controller. The results were that instead of the whole robot dying only one side did. Because of this we concluded that only one motor controller went out and that it was the first in the chain. If the first motor controller went out the rest of the controllers would not be getting any power causing nothing to run. We deduced that something was short circuiting we couldn’t figure out what so we decided to rewire the whole robot.

We made a meeting the next day to rewire the whole robot but when we got there we did some more tests and the robot was working. Because we didn’t do anything to the robot to fix it we still decided to go ahead and rewire. First we undid all the motors, the servos, and the power wires then we moved two motor controllers to a spot where we could access them easier. We made a plan on how to wire it the easiest way.

Then we started with connecting all the battery wires and the wires that connect the motor controllers to the NXT. Since our first controller was one for the servos and our other three were for the motors we gave the motor ones the battery priority by having them closer to the battery servos need less power so they could be further away. The wires that carry the command are running the opposite way than the power wires.

We started doing the drive motors and thought that it would be easiest to put each motor in separate ports instead of having both drive motors on each side in the same port. So we started doing it that way but as we were putting in the other motors we found that one of the motor ports was stripped in the motor controller. Because of the design we cannot remove the motor controller easily because it was one that is in the center we would have to remove one other controller to get it out. So we doubled up the drive motors to open up some more space.

One of the last things we did was to connect the servos to their proper ports and connected the switch and wired it to the motor controllers and to the Samantha unit. We also put two plastic shields to protect the wires. We ran a couple tests and it was working we were able to score our first ball in the small scoring goal.

We have encountered a recurring problem within the drive system of the robot. If a driver is moving the robot at full speed in one direction then quickly reverses the direction of the robot to full power in the other direction, the robot’s drive motors will cut out and the robot will not move again until a full reboot of the main power is performed. Due to this problem, the robot was taken to a team member’s house over the weekend for troubleshooting.

January 3rd

The troubleshooting began with a replication of the problem to be sure it wasn’t a strange fluke during the previous meeting. From there, the team member disconnected one set of motor wires from the motor controller and moved them to a second motor controller not housed within the robot, then wired a makeshift power jump to this second controller, making sure to disconnect the rest of the motor controllers in the main daisy chain. From here, they tested for the problem again. This time, only one side of the robot, the one plugged into the new motor controller, encountered the same problem, a killing of all power to the motors. This showed a possible issue with the motor wires on that side.

The team member then replaced the motor wires on that side with brand new wires to test. After a repeat of the same test, it was shown that not even this fixed the problem. They then tested the continuity of the wires for all four motors with a multimeter. This test proved that all four motors were receiving power correctly. They then plugged all four motors into the external motor controller in pairs and jumped the main power circuit to this controller, disconnecting all of the main daisy chain of wires. This bypassed every piece of wiring on the robot to give a final test of the drive system. This test gave the same results, and the team member stopped for the day.

January 4th

After some recommendations by a mentor, the team member tried one more option. The mentor had a theory that the motors were drawing too much amperage from the motor controller, thus tripping the safety switch within the motor controller. The team member activated the teleop and moved the stick on the controller slowly in every direction to test the theory. The robot moved in every direction without encountering the recurring drive problem. This showed the theory was correct by demonstrating that with a lower amperage draw, the robot would drive properly. The solution to the problem is to give each of the motors their own port in the motor controllers. This would require a modification in the code, but it would help. After taking the robot back to the garage, another mentor made the suggestion that they should change the power of the motors in the code first, due to the much simpler process for doing this over the addition of a motor controller.

We tested the limit on the power by putting the robot on a crate and making a quick program that would just spin the wheels forwards and then reverse them. As it was not working we kept putting more and more limit on the power. We then got to a point where we would be going to slow and decided to have the program make the robots wheels do a complete stop before reversing direction. This made the robot last longer but in the end it still died.

We then were wondering if the servo controller was the problem. To check it we unplugged it from the chain and plugged in just the motor controllers. We then tested it on the crate again but it still did not work. We then decided to separate all our motors because our mentor found on the web site that somebody had the same problem. The problem ended up being that when we put two motors in one port they draw more power when they reverse direction.

We knew that we could not separate the motors without adding a new motor controller because one port one controller was not working because it was stripped. So we added another motor controller on top to replace it because it would be very hard to take it out and put a new one back in and we do not have enough time. So we put a new one on and wired it and it works!!! Because of our wiring changes we had to redo our wiring diagram.

We tested it in the end by doing drivers practice where we tested it as we were driving and we were giving our new team mates a chance to drive the robot. Our con conclusion was that the motors were pulling too much power causing some thing in the motor controller to set off making the robot not work.

The supremacy of Khan III

We decided to not use the tube because it vas to heavy and it was hard to make it work. So we came up with a small light bucket that could easily go up or down. This allowed us to only need one linear slide. This gives us more room on the robot and an extra motor to play with.

Our current design has not had as many problems but we still have had a few. The main problems that we have had with this design have been that the bucket that we use to score the balls with has cracked a couple times, that our wiring has had problems, that our gears kept slipping, and that our linear slide was very hard to bring down.

Our bucket we plan to redo with stronger plastic and make it out of one piece of plastic. We separated our motors which has solved most of our wiring problems. We solved our gear skipping problem by putting chain to drive our robot instead of doing it with normal gears.

Slide all the way up

One of our main problems has been our linear slide. Our linear slide had problems going down because there was so much friction that it always got stuck in one part. It was always one part of it that got stuck. So we tried lubricating it with WD40 but it did not help. So we decided to unstring the slide and see if that helped it. We unstrung it and we let it down almost all of it went down but one part did not. So we kept moving the part that did not go down and we could hear a noise like there was dirt in the little balls that bake it slide. But there shouldn’t have been any because the lubrication should have flushed it out.

So we decided to remove a part that we had screwed in there to see if it was that part. The part was there so that we could extend the slide all the way up. Then we lowered it again but it did not help at all. So we decided not to extend the linear slides all the way so that we could still score with the rest. Without that half of the slide we could still score in the tall goal but the dis advantage is that we could not score in the center goal.

We then decided to try to use 50lb fishing wire to raise the slides. The par cord that we used made too much friction exist and the motor strained to extent the linear slides. After a few runs up and down the fishing wire snapped. So we ended up using some string that is not as thick and is slicker than the paracord.

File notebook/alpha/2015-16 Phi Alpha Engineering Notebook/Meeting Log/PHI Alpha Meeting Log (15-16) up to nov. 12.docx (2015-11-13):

July 22-27 2015 (A.V Vex Workshop)

One of several events that our team volunteered at this past summer, was the VEX Robotics workshop. The workshop was planned and executed by several FTC and FRC teams from around our area. This event was a one weeklong workshop, in which kids from all around the Antelope Valley would come and learn about STEM programs and engineering. Our goal was to inspire kids about engineering and to share the values that we have learned through the FIRST program.

This was done in two ways: presentations, and robot design. Each day during the beginning of workshop we had speakers come in from NASA and other engineering companies. These speakers would come in and give a short presentation about an element in engineering, such as how planes are able to fly, and then have a game set up after for them to play to give some hands on learning. For one of the presentations, all of the FIRST teams presented and spoke about their team, the game for that year, and what they went through to build their robot.

During the other part of the day, robot design, the kids were divided up into competition teams. At the beginning of the week, the kids were presented with a game challenge, similar to that in FTC. Throughout the week, the teams worked with the VEX parts to build a robot. On the final day, Saturday, parents were invited to come see their kids compete in a friendly competition. AND IT WAS LOTS OF FUN!!!!!!!!!!!!!!!!:)

Monday – August 17, 2015

Goals: Tonight we are meeting with PHI Omega at their garage to discuss the plans for the AV Fair. The current plan is to bring our robots and last year’s field and demonstrate to the public what robotics is, and get them interested. We will be discussing the particulars such as which team is there at what time, and which members are going. If we have time after discussing the fair, we are going to do some research on how to set up and use the new electronics system.

Accomplishments: We finished planning the schedule for the AV Fair, and assigned team members time shifts. After that, we drove back to our garage and began to play with the electronics. We were nervous that it wouldn’t work at first, but the setup was simpler than expected, and is very well explained.

Plans: During the next meeting, we will be focusing on preparing the robot for the demonstration at the A.V. Fair. We will also attempt to get some motors to turn using the new equipment.

Author: Timothy Bloot

Thursday – August 20, 2015

Goals: Sell Jethawks game tickets, prepare our robot, put a spare parts kit togeher. Experiment with the new phones

Accomplishments: Tonight, two of our members went around door to door selling Jethawks tickets as one of our fundraisers. We talked about our team and how we are a non-profit organization and that we have to make up some of the money ourselves.. through fundraisers. The rest of our members prepared our old robot from last year for our outreach at the Antelope Valley Fair. We had to re-install a trial version of Robot C since we wiped our old license out when we upgraded our computers. We put together a "go" kit, to help us fix any issues during the fair. We spent the rest of the night preparing our phones for the new season. The instructions from the first website were invaluable; we would have never figured out how to configure them on our own.

Discoveries: We had to re-install a trial version of Robot C since we wiped our old license out when we upgraded our computers. Once we installed the Software we were able to load our old programs and return the robot to good working order.

Plans: get a powered setup of the new hardware and begin programming

Author: Cierra Bachtelle

Saturday – August 22, 2015 (AV Fair Outreach Night)

Author:

Thursday – August 27, 2015 (Alpha and Omega Meeting)

Goals: Get a powered setup of the new hardware and begin programming.

Accomplishments: We had a group meeting tonight, our mentor set our objectives, which included starting a bill of materials, figuring out the new programming ways, breaking down the old robot, and establishing roles and responsibilities for the new year. Tonight we striped our robot down to just the chassis, so we could prepare for next year’s challenge. Our mentor cried when we took apart the robot because he lived with it for years. Tonight we made an objective to set up the new electronics system and attempt to get the two phones to communicate with each other. Along with the phones, we also began to disassemble last year’s robot, to much of our mentor’s sadness. Throughout the beginning of the meeting, we had to check and double check the setup and reconnect things until finally we got the electronics to communicate with each other. Our next step is to integrate our own programming into the new system.

Discoveries: Tonight we learned and figured out some of the new programming ways. We learned how to set up the java program. So now, next meeting our goal is to make our own program this time. Just a basic program to move motors and other things likes that.

Plans: our plans for tonight are to build the Bost that we will need for the next season. We put together our bom based off our budget with money to spare for things we will need for spares. We looked for spare parts and new equipment and put it all on a list for us to buy and how much it will cost.

Author: Cierra Bachtelle

Saturday – September 12, 2015 (FTC Kick-off Barbeque)

The wait is finally over! Today both teams, Alpha and Omega, met and had a kick off barbeque. We had some amazing food, made by Mr. McMillan, and watched the game animation for this season. Res-Q looks like a challenging game, but will rise to the occasion! With nerves shaking and our minds racing, we began to discuss some ideas for robot design and what we want to accomplish. We also went over the rules and penalties for this year’s game. Both teams are super excited and ready to get started!

Thursday – September 17, 2015

Goals:

Accomplishments:

New Knowledge:

Plans: B.O.M., team rules, notebook, meeting log, software section, 3D printer set up, basic chassis.

Author: Cierra Bachtelle

Monday – September 21, 2015

Goals: B.O.M., team rules, notebook, meeting log, software section, 3D printer set up, basic chassis.

Accomplishments: We got the motors to spin on the practice bot, finished the B.O.M, we started on the software for the 3D printer, we revised our order list, did more programing, taught the new team members more programing hardware and notebook.

Discoveries: Pushing forward on both of the robot's control sticks caused one wheel to spin forward and the other to spin in reverse, but we fixed it by switching the wheel's spin direction.

Plans: Our future plans for the next meeting are to get the 3D printer fully operational, the robot running on four wheel drive, finish discussing the team rules, and finally to start prototyping arms and buckets.

Author: Joe Baughman

Thursday – September 24, 2015

Goals: notebook software section 3d printer basic chassis redesign the chassis set up calendar arm ideas different ideas for the chassis and wheels we went over the requirements for the robot

Accomplishments: We decided on what your practice bot was going to be. We decided on a compromise between the cracken chassis and the low rider chassis, which we had two separate groups working on and we decided to combine our two ideas and made something that should work, we might have to make a few adjustment, but the basic design is there. We also began working on getting wiring re setup, and getting that reorganized and not messy. We worked on the wheels and decided on tread as our final design so we can climb the mountain.

Discoveries: We found out that some designs of wheels weren’t very good so we decided against doing a three wheel bot and that was unexpected because most of our team members had expected one design to work but that did not. If we had a low rider chassis the bot would get high sighted and not be able to move so due to that discovery we adjusted our plan and made a high rider kraken style chassis bot

Plans: Get the tread on the bot so that we can work on driver practice and finish doing wiring layouts and getting the cord power distribution module hooked up and turning the two wheel drive to four wheel drive hooked up to the two motors and starting the mount for the arm

Author: Luke McMillian

Monday – September 28, 2015

Goals: Get the tread on the bot so that we can work on driver practice and finish doing wiring layouts and getting the cord power distribution module hooked up and turning the two wheel drive to four wheel drive hooked up to the two motors and starting the mount

Accomplishments: rookie programmer read and understood the first three lessons from module three and got the android studio along with git hub also the lieutenant programmer was able to start programming color sensors along with acoustic sensors. To add we were able to get our prototype two wheel chassis, hardware also did prototyping robotic arm.

Discoveries: we discovered working arm techniques like hooks that shot out to grab the bar and pull themselves up with a bucket that collected balls and blocks and dumped them into the scoring buckets.

Plans: Get the tread on the bot so that we can work on driver practice and finish doing wiring layouts and getting the cord power distribution module hooked up and turning the two wheel drive to four wheel drive hooked up to the two motors and starting the mount

Author: Immanuel Lawhon

Thursday – October 1, 2015

Goals: Get the tread on the bot so that we can work on driver practice and finish doing wiring layouts and getting the cord power distribution module hooked up and turning the two wheel drive to four wheel drive hooked up to the two motors and starting the mount

Accomplishments: software; I learned lots of stuff tonight! I know how to program tank drive and arcade mode.. but it wasn't until tonight that I really knew what I was doing, and I now know how to teach it properly. All because I took the time out to look on the FIRST website and read up on it more. -Kayla.

Hardware; we decided on an initial design for our arm and bucket. This design consists of a conveyor belt that feeds into a side dumping bucket. Also, we brainstormed an idea for lifting our bot in the end game. The design consists of a winch with a wire that runs up to a hook. The hook is to be Velcroed onto an extendable arm that would deploy during the end game. - Timothy Bloot

Discoveries: The hardware team made some unexpected changes in arm design. We decided to try a solid mounted bucket that would dump rather than a bucket that would move on a rotational arm.

Plans: Software: learning the color sensor and gyro sensor. Making an arcade drive program. Hardware: make another cardboard bucket with correct measurements, and mount the winch. Design a model spool and test print. Figure out how to save the spool model into the ekocycle format.

Author: Jeremiah Baughman

Monday – October 5, 2015

Goals: Software: learning the color sensor and gyro sensor. Making an arcade drive program. Hardware: make another cardboard bucket with correct measurements, and mount the winch. Design a model spool and test print. Figure out how to save the spool model into the ekocycle format.

Accomplishments: the rookie programmer immanuel lawhon was able to set up colour sensor programs on his computer and experiment with more coding in arcade mode and also tank mode and coming up with arm ideas and chassis ideas. Lieutenant Kayla Bachtelle made a program that contains the following tasks: the use of two motors in arcade mode, and a motor for an arm using the game-pads A and B. we resigned the bucket model to be smoother and to hold more game elements, and reach farther out of dimensions, by releasing a trap door to guide the game elements into the buckets on the ramp. We received the field kit in the past week and started to examine some of the parts and setup, such as the buckets and the ramp.

Discoveries: there was a temperature error while attempting to print our first 3D model. Also the hardware team made an unexpected change to the bucket design after some examination of the field elements.

Plans: Get a working practice robot, test the software on the bot,

Author: Cierra Bachtelle/Immanuel Lawhon

Thursday – October 8, 2015

Goals: Get a driving practice robot, test the software on the bot., build a bucket prototype

Accomplishments: We got the tread set up in the bot, and we got the bot to move using out teleop, we built a ballistic prototype for a bucket

Discoveries:

Plans:

Author:

Thursday – October 12, 2015

Goal:

Accomplishments: we figured our how to move the robot the correct way, driver practice, got half of the field set up,

Discoveries:

Plans: get tables reset up and get them organized, set up the rest of the field,

Author: Cierra Bachtelle

Thursday – October 15, 2015

Goals: Get tables reset up and get them organized, set up the rest of the field, get the notebook caught up. Work on more designs for the robot, such as arms and drive.

Accomplishments: Tonight we got more of our field set up, and updated more of the notebook. The hardware team did a major rehall on the robot's chassis and drive system. The robot now has a tank like tread setup so that it may have a higher chance of climbing the ramp.

Discoveries: we discovered that our original design for our drive was not sufficient for this years game, so we decided to overhaul it. We had to come up with creative ways to put the field together since we thought some pieces were missing, and we could not find some of the necessary tools, so we improvised and got the job done.

Plans: Our plans for next Monday are to finish assembling the mountain and continue with the reconstruction of the robot. For software, we will continue to work with the teleop programs as well as working with the sensors.

Author: Timothy Bloot

Monday – October 19, 2015

Goals: Our plans are to finish assembling the mountain and continue with the reconstruction of the robot. For software, we will continue to work with the teleop programs as well as working with the sensors.

Accomplishment: Hardware was able to set up most of the field. Also we were able to redesign the tread and add rubber traction. To add the hardware was able to rewire the robot after redesigning the tread. Lieutenant Kayla worked a lot with the color sensors along with setting up a few more computers. While rookie Immanuel worked on note booking and a few concepts for software.

Discoveries: we discovered that our programing for the color sensors was a little off so we were working on programming color sensors to a device interface

Plans:

Author: Cierra Bachtelle/Immanuel Lawhon

Monday – October 22, 2015

Goals: We had plans to get the robot to move, because we took apart the drive train and we will need to rewire it tonight.

Accomplishments: We got the robot to move. And we started making arm prototypes to score in the lower scoring goal. We came up with a design for scoring also we made the tread work along with the rubber inserts and wired. SOFTWARE: software was able to get the bot moving again but we had to change tank drive we made single stick arcade drive. NOTEBOOK: the note book revision team was able to accomplish working on space filler for our meeting log.

Discoveries: We found that the current tread drive train can not make the robot get over the ramp rods. When we rewired the robot our drive was reversed so we fixed that. We found that pour robot can not make it up the ramp on its own.

Plans: Build a folding arm that can reach the middle/ lower scoring goal. Also build a hook that can reach the high pull-up beam to help us reach the top of the ramp. Write team bios for the notebook and finish the meeting logs.

Author: Immanuel Lawhon/Scott Kidman

Monday – October 26, 2015

Goals: Hardware goals for tonight are to find a good place to mount our scoring arm, as well as a place for the linear slide. Software plans are to finish the arcade drive program and start working on autonomous programming. The notebook team plans to write down the team bios, and continue work on the notebook formatting.

Accomplishments: The hardware team mounted the base for the scoring arm. Along with that they also mounted the linear slide for getting the hook all the way up to the lift bar for end game. The software team learned how to program autonomous movements as well as teleop programs. The notebook team for the night worked on writing down team bios, and also continued designing formats for the notebook.

Discoveries: our original mount for the winch slide was at too steep of an angle as well as being out of dimensions, so we redesigned and built the arm to fit withing dimensions. The software team is running into some minor issues with programing servos in autonomous, but they are close.

Plans: For next week, hardware plans to build the bucket for scoring elements and mount the hook and winch for end game strategy. Software plans to write some autonomous programs and work on arcade drive.

Author: Timothy Bloot

Thursday – October 29, 2015

Goals: Hardware goals for tonight include designing the bucket and building a prototype, remount the scoring arm, and find a new mounting spot for the zip line servo. Finally, we need to assemble and mount the two winches for the end game. Software goals include check out the challenge video of this year again set up autonomous strategies, then figure out what our scoring would be. Also, we need to fix the android phones, and then move the robot in arcade drive. we would also like to order some much needed parts.

Accomplishments: We set the goals of what we want to do for the autonomous period and figured out what the scoring would be. We fixed the problem on the android phones!!!!! Hardware was able to assemble an arm for knocking down zip liners and for scoring except we have to re figure an arm. Software was able to learn more and also make a few autonomous programs. Notebook was able to do more note booking for past events.

Discoveries: the score would be 50 if we do want we wanted to do. We discovered that we mounted the zip-line servo. We also had to rebuild the arm joint because of a design change.

Plans: figure out how to use the color sensor and the gyro sensor.

Author: Immanuel Lawhon/ Tim Bloot

Thursday – November 5, 2015

Goals: To get a retracting winch to pull our selves up. Get the final touches on the field. Get autonomous working smoothly and getting the rest of arcade drive set up. Also get more of the notebook events and sections done.

Accomplishments: Hardware was able to get a retracting winch done. We were able to finish off another more simple winch for the linear slide. Hook for the pull up bar that is attached to the retractable winch. Removed the short arm to score on the ramp and built a custom flipper for the zip-liners. Software was able to get some autonomous done and tested when driving in a square. And we were able to start gyro sensors. In the Notebook tonight we got the outreach section up to date, we also got our team vision finished.

Discoveries: Hardware we removed our small one stage scoring arm so that we can fit a winch in its place and because we didn’t have enough time to finish both arms and that’s another reason we removed the small arm. Software learned how to strip wire.

Plans: Next week we plan to wire and get the long arm fully operational so we can pull our robot off the floor, start driver practice, learn gyro. Get the rest of the notebook up to date. And also take pictures of our robot and team members for the bios.

Author: Cierra Bachtelle/Immanuel Lawhon

Monday – November 9, 2015

Goals: Finish major hardware design, wright a competition ready program with the ability to move all the attachments on the robot,

Accomplishments: Software we made a competition ready teleop that we just need to test bout, it contains the following tasks; motorized arm for right joy stick, arced drive on left joy stick, one servos using A and b and the other servo using x and y. Hardware we attached the final design for the climber levers on the side of the bot we had to cut a few pieces of Tetirx to make it turn out smoothly, we created mounting space so that we can mount our winch that we made last meeting, we modified our lift hook to be stronger.

Discoveries: Hardware had to edit Tetirx parts to make the new arm fit,

Plans: Finish wiring the new elements on the robot, which include three motors and two servos.

Author: Cierra Bachtelle

Thursday – November 12, 2015

Goals: Finish wiring the bot, finish mounting the end game hook, update the notebook, set up fields, build a practice robot,

Accomplishments: The hardware team finished wiring the new elements. The software team did some research on game rules as sensors. As a bonus, we celebrated a teammate's birthday today, and had cake!

Discoveries: the hardware team discovered that they need to remount a new design for a scoring arm.

Plans: check the robot for appliance to the rules. Because we are still behind the next meeting will be a two hour hardware craze and then the last hour we will do complete software

Author: Tim Bloot

452 PHI Alpha 452

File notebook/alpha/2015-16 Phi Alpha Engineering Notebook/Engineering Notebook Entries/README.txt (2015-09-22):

Be sure to save ALL files as .docx (readable by Microsoft word 2007-2013) 
this will need to be changed when ANY new document is made

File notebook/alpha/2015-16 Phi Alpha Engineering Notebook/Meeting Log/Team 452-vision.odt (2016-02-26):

Power through Higher Innovation

What is our vision? We are a world class, diverse group of home-schooled high school students banding together to further education in STEM leadership and community outreach through robotics and the FIRST technical challenge while exhibiting the principles of gracious professionalism and of our Lord Jesus Christ.

Colossians 3:17

“And whatever you do, whether in word or deed, do it all in the name of the Lord Jesus, giving thanks to God the Father through Him.”

452 PHI Alpha 452

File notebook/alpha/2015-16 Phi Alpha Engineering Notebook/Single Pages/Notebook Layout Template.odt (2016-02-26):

Notebook Template

1. Cover Page
2. Team Summary
3. Business Plan
4. Team Bios
5. Meeting Log
6. Engineering Section
  1. Hardware Section
  2. Software Section
7. Public Relations Section
  1. Outreach Activities
  2. Funds
    1. Sponsors
    2. Fund raising events

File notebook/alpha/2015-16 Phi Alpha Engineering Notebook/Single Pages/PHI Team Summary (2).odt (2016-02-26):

The Origin of PHI

PHI Robotics is a Christian garage team that has been around since before FTC started. In the beginning, we were one team, PHI Robotics. After several years, our team grew substantially so that we chose to split into two sister teams, PHI Alpha, and PHI Omega. Our two teams work together for fund raising and outreach, as well as sharing software and hardware ideas.

Good Times

This year, we have several new members on the team. Because of this, the beginning of the was a lot of training. Our favorite part of this was getting to know each other, and figuring out what each person likes to do.

During the summer, we focus on reaching out to the community to share about FIRST robotics and about our team. One major event that we put on, with other teams from our area, is the VEX workshop. Kids from the community come each day, and learn about engineering programs, and build robots. This event is a LOT of fun, and we have a great time hanging out with the kids.

Of of our favorite moments of this competitive season would have to be when we first got the robot to move. We were so excited that we had finally been able to communicate with the system! We knew that the work was just beginning, but it was a major breakthrough and got us excited to see what else we can do.

Our first competition was very stressful. The robot was having problems, and one of our team members was hurt. The day was a challenge, and a learning experience. By a true miracle we ended up being the fourth alliance captain, but did not qualify. We had fun, and it was a real morality booster for our team.

Getting Started

- Who are we? (pg. )
- PHI Robotics Kickoff (pg. )
- Team Business Plan

Meetings

- It's Alive! (pg. )
- First Autonomy Movement (pg. )

Hardware

- The Two-Face Protocol (pg. )
- Robot Versions (pg. )
- CAD Modeling and design (pg. )

Programming

- Our Teleop (pg. )
- Working with Java

PHI Outreach

- VEX Robotics Workshop
- Antelope Valley Fair Booth

Funding

- Our sponsors (pg. )
- Jethawks Event (pg.)

452 PHI Alpha 452

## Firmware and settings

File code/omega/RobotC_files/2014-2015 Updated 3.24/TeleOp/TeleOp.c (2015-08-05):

#pragma config(Hubs,  S1, HTMotor,  HTMotor,  HTMotor,  HTServo)
#pragma config(Sensor, S1,     ,               sensorI2CMuxController)
#pragma config(Sensor, S2,     Gyro,           sensorI2CHiTechnicGyro)
#pragma config(Sensor, S3,     mux,            sensorI2CCustom)
#pragma config(Sensor, S4,     htspb,          sensorI2CCustom)
#pragma config(Motor,  mtr_S1_C1_1,     leftFront,     tmotorTetrix, openLoop)
#pragma config(Motor,  mtr_S1_C1_2,     leftRear,      tmotorTetrix, openLoop, encoder)
#pragma config(Motor,  mtr_S1_C2_1,     intake,        tmotorTetrix, openLoop)
#pragma config(Motor,  mtr_S1_C2_2,     rightRear,     tmotorTetrix, openLoop, reversed, encoder)
#pragma config(Motor,  mtr_S1_C3_1,     rightFront,    tmotorTetrix, openLoop, reversed)
#pragma config(Motor,  mtr_S1_C3_2,     lift,          tmotorTetrix, openLoop, encoder)
#pragma config(Servo,  srvo_S1_C4_1,    inputstop,            tServoStandard)
#pragma config(Servo,  srvo_S1_C4_2,    hook1,                tServoStandard)
#pragma config(Servo,  srvo_S1_C4_3,    hook2,                tServoStandard)
#pragma config(Servo,  srvo_S1_C4_4,    irTurret,             tServoStandard)
#pragma config(Servo,  srvo_S1_C4_5,    ultraTurret,          tServoStandard)
#pragma config(Servo,  srvo_S1_C4_6,    output,               tServoStandard)
//*!!Code automatically generated by 'ROBOTC' configuration wizard               !!*//

#define ir msensor_S3_1
#define touch msensor_S3_2
#define accel msensor_S3_3
#define ultraSonic msensor_S3_4
//*!!Code automatically generated by 'ROBOTC' configuration wizard               !!*//

/////////////////////////////////////////////////////////////////////////////////////////////////////
//
//                           Tele-Operation Mode Code Template
//
// This file contains a template for simplified creation of an tele-op program for an FTC
// competition.
//
// You need to customize two functions with code unique to your specific robot.
//
/////////////////////////////////////////////////////////////////////////////////////////////////////

#include "JoystickDriver.c"  //Include file to "handle" the Bluetooth messages.
#include "hitechnic-sensormux.h"
#include "hitechnic-superpro.h"
#include "lego-touch.h"
#include "Buttonmap.h"
int deadband = 10;
float driveFraction = 1.0;
bool driving = false;
bool runIntake = true;
bool closeOverride = false;
int driveStyle = 0;
task AwesomeDrive;
task LameDrive;
task Arm;
task Buttons;

/////////////////////////////////////////////////////////////////////////////////////////////////////
//
//                                    initializeRobot
//
// Prior to the start of tele-op mode, you may want to perform some initialization on your robot
// and the variables within your program.
//
// In most cases, you may not have to add any code to this function and it will remain "empty".
//
/////////////////////////////////////////////////////////////////////////////////////////////////////

void initializeRobot()
{
	servo[output] = 130;
	servo[hook1] = 0;
	servo[hook2] = 255;
	servo[irTurret] = 255;

	//HTSPBsetupIO(htspb, 0b00000001);
	//HTSPBwriteIO(htspb, 0b00000001);


	return;
}


/////////////////////////////////////////////////////////////////////////////////////////////////////
//
//                                         Main Task
//
// The following is the main code for the tele-op robot operation. Customize as appropriate for
// your specific robot.
//
// Game controller / joystick information is sent periodically (about every 50 milliseconds) from
// the FMS (Field Management System) to the robot. Most tele-op programs will follow the following
// logic:
//   1. Loop forever repeating the following actions:
//   2. Get the latest game controller / joystick settings that have been received from the PC.
//   3. Perform appropriate actions based on the joystick + buttons settings. This is usually a
//      simple action:
//      *  Joystick values are usually directly translated into power levels for a motor or
//         position of a servo.
//      *  Buttons are usually used to start/stop a motor or cause a servo to move to a specific
//         position.
//   4. Repeat the loop.
//
// Your program needs to continuously loop because you need to continuously respond to changes in
// the game controller settings.
//
// At the end of the tele-op period, the FMS will autonmatically abort (stop) execution of the program.
//
/////////////////////////////////////////////////////////////////////////////////////////////////////
task AwesomeDrive()
{
	//Define storage variables
	int rawX, rawY;
	float shapedX, shapedY;
	float leftPower, rightPower;
	driveStyle = 0;

	while (true)
	{
		//Get joystick data
		getJoystickSettings(joystick);

		//Check if the joystick is being used on any axis
		if (abs(joystick.joy1_x1) > deadband)
			rawX = joystick.joy1_x1 - (sgn(joystick.joy1_x1) * deadband); //Set variables and subtract deadband from total to avoid jump
		else
			rawX = 0;
		if (abs(joystick.joy1_y1) > deadband)
			rawY = joystick.joy1_y1 - (sgn(joystick.joy1_y1) * deadband); //Set variables and subtract deadband from total to avoid jump
		else
			rawY = 0;

		//Shape the powers based on equation: y = (2/225)(x*abs(x))+(14/45)x
		shapedX = 0.0088888888888889 * (rawX * abs(rawX)) + 0.3111111111111111 * rawX;
		shapedY = 0.0088888888888889 * (rawY * abs(rawY)) + 0.3111111111111111 * rawY;
		//shapedX = (float)(2/225) * (rawX * abs(rawX)) + (float)(14/45) * rawX;
		//shapedY = (float)(2/225) * (rawY * abs(rawY)) + (float)(14/45) * rawY;

		//Determine power of each side by slowing one side and increasing the other appropriately
		leftPower = shapedY - shapedX/2;
		rightPower = shapedY + shapedX/2;

		//Finally, set the power to the motors
		motor[leftFront] = leftPower * driveFraction;
		motor[leftRear] = leftPower * driveFraction;
		motor[rightFront] = rightPower * driveFraction;
		motor[rightRear] = rightPower * driveFraction;

		if (abs(leftPower) > 0 || abs(rightPower) > 0)
			driving = true;
		else
			driving = false;

		if (joy1Btn(BTN_SELECT))
		{
			wait10Msec(30);
			StartTask(LameDrive);
			break;
		}
	}
}

task LameDrive()
{
	//Define storage variables
	int rawLeft, rawRight;
	float shapedLeft, shapedRight;
	driveStyle = 1;

	while (true)
	{
		//Get joystick data
		getJoystickSettings(joystick);

		//Check if the joystick is being used on any axis
		if (abs(joystick.joy1_y1) > deadband)
			rawLeft = joystick.joy1_y1 - (sgn(joystick.joy1_y1) * deadband); //Set variables and subtract deadband from total to avoid jump
		else
			rawLeft = 0;
		if (abs(joystick.joy1_y2) > deadband)
			rawRight = joystick.joy1_y2 - (sgn(joystick.joy1_y2) * deadband); //Set variables and subtract deadband from total to avoid jump
		else
			rawRight = 0;

		//Shape the powers based on equation: y = (2/225)(x*abs(x))+(14/45)x
		shapedRight = 0.0088888888888889 * (rawLeft * abs(rawLeft)) + 0.3111111111111111 * rawLeft;
		shapedLeft = 0.0088888888888889 * (rawRight * abs(rawRight)) + 0.3111111111111111 * rawRight;

		//Finally, set the power to the motors
		motor[leftFront] = shapedLeft * driveFraction;
		motor[leftRear] = shapedLeft * driveFraction;
		motor[rightFront] = shapedRight * driveFraction;
		motor[rightRear] = shapedRight * driveFraction;

		if (abs(shapedLeft) > 0 || abs(shapedRight) > 0)
			driving = true;
		else
			driving = false;

		if (joy1Btn(BTN_SELECT))
		{
			wait10Msec(30);
			StartTask(AwesomeDrive);
			break;
		}
	}
}

task Arm()
{
	int count = 0;
	float lightVal = 0;
	float lightAvg = 0;
	bool bucketFull = false;
	bool counted = false;
	while(true)
	{
		getJoystickSettings(joystick);
		if (joy1Btn(BTN_LB) && !joy1Btn(BTN_LT))
			motor[lift] = 75;
		else if (joy1Btn(BTN_LT) && !joy1Btn(BTN_LB))
			motor[lift] = -75;
		else
			motor[lift] = 0;

		if (joy1Btn(BTN_RB) && !joy1Btn(BTN_RT) && runIntake)
			motor[intake] = 100;
		else if (joy1Btn(BTN_RT) && !joy1Btn(BTN_RB) && runIntake)
			motor[intake] = -100;
		else
			motor[intake] = 0;

		lightVal = HTSPBreadADC(htspb, 0, 10);
		//writeDebugStreamLine("Count: %d", count);
		//writeDebugStreamLine("Avg: %d", lightAvg);
		//writeDebugStreamLine("Val: %d", lightVal);
		if (lightVal > (lightAvg - 40) && !counted && time1[T3] > 1200)
		{
			count += 1;
			counted = true;
			writeDebugStreamLine("Count: %d", count);
			//writeDebugStreamLine("Avg: %d", lightAvg);
			//writeDebugStreamLine("Val: %d", lightVal);
			ClearTimer(T3);
		}
		else if (counted && lightAvg < (lightVal + 15))
		{
			counted = false;
		}
		else if (time1[T2] > 500)
		{
			lightAvg = lightVal;
			ClearTimer(T2);
		}
		if (count == 5)
		{
			//bucketFull = true;
			ClearTimer(T1);
			count = 0;
		}
		if (time10[T1] > 300 && bucketFull)
		{
			runIntake = false;
			bucketFull = false;
		}
		if (TSreadState(touch) == 1 && !closeOverride)
			servo[inputstop] = 130;
		else if (TSreadState(touch) == 0 && !closeOverride)
			servo[inputstop] = 235;
		if (time1[T4] > 5000)
			closeOverride = false;
	}
}

task Buttons()
{
	while (true)
	{
		getJoystickSettings(joystick);

		if (joy1Btn(BTN_A))
		{
			if (servo[output] < 190)
				servo[output] = 244;
			else
				servo[output] = 130;
			runIntake = true;
			wait10Msec(40);
		}
		if (joy1Btn(BTN_Y))
		{
			closeOverride = true;
			ClearTimer(T4);
			if (servo[inputstop] < 190)
				servo[inputstop] = 235;
			else
				servo[inputstop] = 130;
			wait10Msec(40);
		}
		if (joy1Btn(BTN_B))
		{
			runIntake = true;
		}
		if (joy1Btn(BTN_X))
		{
			if (servo[hook1] > 180)
			{
				servo[hook1] = 0;
				servo[hook2] = 255;
			}
			else
			{
				servo[hook1] = 255;
				servo[hook2] = 0;
			}
			wait10Msec(40);
		}
	}
}


task main()
{
	initializeRobot();

	waitForStart();   // wait for start of tele-op phase

	clearDebugStream();
	StartTask(AwesomeDrive);
	StartTask(Arm);
	StartTask(Buttons);

	long messageCountPrev = 0;
	while (true)
	{
		if (messageCountPrev == ntotalMessageCount)
		{
			StopTask(AwesomeDrive);
			StopTask(Arm);
			StopTask(Buttons);
			StopTask(LameDrive);

			motor[mtr_S1_C2_1] = 0;
			motor[mtr_S1_C2_2] = 0;
			motor[mtr_S1_C3_1] = 0;
			motor[mtr_S1_C3_2] = 0;
			motor[mtr_S1_C4_1] = 0;
			motor[mtr_S1_C4_2] = 0;

			wait10Msec(100);

		StartTask((driveStyle == 0) ? AwesomeDrive : LameDrive);
			StartTask(Arm);
			StartTask(Buttons);
		}

		messageCountPrev = ntotalMessageCount;
		wait10Msec(100);
	}

}

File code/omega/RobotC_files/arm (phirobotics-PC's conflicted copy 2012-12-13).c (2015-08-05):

//=============================================================================
// Function: Move()
//
// Description:
//    This function will turn the arm the degrees specified in "degrees".
//
// Parameters: degrees = degrees to rotate arm, Positive is forward,
//                        Negative is backward
//=============================================================================
void Arm( float degrees, float max_speed )
{
  float COUNTS_PER_INCH = 2.05;
  int countDistance;
  int direction = 1;
  int motorSpeed = 0;
  int MAX_ENCODER_SPEED  = 70;
  nMotorPIDSpeedCtrl[Arm_motor] = mtrSpeedReg;
	nMaxRegulatedSpeed12V = 1000;
	float encoderArm = nMotorEncoder[Arm_motor];

  // Determine direction. Set to negative for backwards
  if( degrees > 0 )
  {
    direction = -1;
  }
  // Calculate the degrees to travel in encoder counts
  countDistance = abs(degrees) * COUNTS_PER_INCH;

  // remove the backlash and freeplay from the motors before zeroing the encoders by commanding
  // a very low power for a short time

  motorSpeed = 5;
  motor[Arm_motor] = direction * motorSpeed;

  wait1Msec(10);

  if ( (int)(abs(max_speed)) < MAX_ENCODER_SPEED) {
    MAX_ENCODER_SPEED = (int)max_speed;
  }

  // reset the motor encoders to zero
  nMotorEncoder[Arm_motor] = 0;

  motor[Arm_motor] = direction * MAX_ENCODER_SPEED;

  while (abs(nMotorEncoder[Arm_motor]) < countDistance) //while the encoder wheel turns one revolution
  {
    // This condition waits for motors D & E to come to an idle position. Both motors stop
    // and then jumps out of the loop
  	encoderArm = nMotorEncoder[Arm_motor];

		wait10Msec(50); // give the Messagecount time to change it changes every 50ms

		if(encoderArm == nMotorEncoder[Arm_motor]) // checks to see if the Message change if has not it is Disconnected
		{
			motor[Arm_motor] = 0;
		}
  }

  //motor[Arm_motor] = -direction*50;

  wait10Msec(1);

  motor[Arm_motor] = 0;

  // reset the back motor encoders to zero
  nMotorEncoder[Arm_motor] = 0;

} // End of Move()

//-----------------------------------------------------------------------------
//                              End of file
//-----------------------------------------------------------------------------

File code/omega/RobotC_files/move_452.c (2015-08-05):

//=============================================================================
// Function: Move()
//
// Description:
//    This function will drive the robot the distance specified in "distance".
//
// Parameters: distance = distance in inches, Positive is forward,
//                        Negative is backward
//=============================================================================
void Move( float distance, float max_speed )
{
		nMotorPIDSpeedCtrl[R_Rear]= mtrSpeedReg;
		nMotorPIDSpeedCtrl[L_Rear]= mtrSpeedReg;
	//	nMotorPIDSpeedCtrl[F_L]= mtrSpeedReg;
	//	nMotorPIDSpeedCtrl[F_R]= mtrSpeedReg;
	nMaxRegulatedSpeed12V = 1000;
  float COUNTS_PER_INCH = 222.22;
  int countDistance;
  int direction = 1;
  int motorSpeed = 0;
  int MAX_ENCODER_SPEED  = 70;
	float Sum_left;
	float Sum_right;

  // Determine direction. Set to negative for backwards
  if( distance < 0 )
  {
    direction = -1;
  }
  // Calculate the distance to travel in encoder counts
  countDistance = abs(distance) * COUNTS_PER_INCH;

  // remove the backlash and freeplay from the motors before zeroing the encoders by commanding
  // a very low power for a short time

  motorSpeed = 5;
  motor[Front_left] = direction * motorSpeed;
  motor[R_Rear] = direction * motorSpeed;
  motor[L_Front] = direction * motorSpeed;
  motor[R_Front] = direction * motorSpeed;
  wait1Msec(10);

  if ( (int)(abs(max_speed)) < MAX_ENCODER_SPEED) {
    MAX_ENCODER_SPEED = (int)max_speed;
  }

  // reset the motor encoders to zero
  nMotorEncoder[L_Rear] = 0;
  nMotorEncoder[R_Rear] = 0;

//  nMotorEncoderTarget[F_L] = countDistance;
 // nMotorEncoderTarget[F_R] = countDistance;

  motor[L_Rear] = direction * MAX_ENCODER_SPEED;
  motor[R_Rear] = direction * MAX_ENCODER_SPEED;
  motor[L_Front] = direction * MAX_ENCODER_SPEED;
  motor[R_Front] = direction * MAX_ENCODER_SPEED;


  while (abs(nMotorEncoder[L_Rear])<  countDistance && abs(nMotorEncoder[R_Rear])<  countDistance) //while the encoder wheel turns one revolution
  {
    wait10Msec(25);
    Sum_left = (abs(nMotorEncoder[L_Rear]));
    Sum_right = (abs(nMotorEncoder[R_Rear]));

    if (Sum_left > Sum_right)
    {
      motor[R_Front] = direction * MAX_ENCODER_SPEED + 30;
    	motor[R_Rear] = direction * MAX_ENCODER_SPEED + 30;
  }
    	else if (Sum_left < Sum_right)
    	{
    		motor[L_Front] = direction * MAX_ENCODER_SPEED + 30;
    		motor[L_Rear] = direction * MAX_ENCODER_SPEED + 30;
  }

    }

  motor[L_Rear] = -direction*50;
  motor[R_Rear] = -direction*50;
  //motor[F_L] = -direction*50;
 // motor[F_R] = -direction*50;

  wait10Msec(1);

  motor[L_Rear] = 0;
  motor[R_Rear] = 0;
 // motor[F_L] = 0;
 //motor[F_R] = 0;

  // reset the back motor encoders to zero
 // nMotorEncoder[F_L] = 0;
 //// nMotorEncoder[F_R] = 0;

} // End of Move()

//-----------------------------------------------------------------------------
//                              End of file
//-----------------------------------------------------------------------------

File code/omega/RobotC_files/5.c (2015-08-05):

#pragma config(Hubs,  S1, HTMotor,  HTMotor,  HTMotor,  HTServo)
#pragma config(Sensor, S1,     ,               sensorI2CMuxController)
#pragma config(Sensor, S2,     Gyro,           sensorI2CHiTechnicGyro)
#pragma config(Sensor, S3,     IR,             sensorHiTechnicIRSeeker600)
#pragma config(Sensor, S4,     sonar,          sensorNone)
#pragma config(Motor,  mtr_S1_C1_1,     Right_Side,    tmotorTetrix, openLoop, reversed, encoder)
#pragma config(Motor,  mtr_S1_C1_2,     Left_Side,     tmotorTetrix, openLoop, encoder)
#pragma config(Motor,  mtr_S1_C2_1,     Block_Arm,     tmotorTetrix, openLoop)
#pragma config(Motor,  mtr_S1_C2_2,     Flag_Arm,      tmotorTetrix, openLoop, reversed)
#pragma config(Motor,  mtr_S1_C3_1,     motorH,        tmotorTetrix, openLoop)
#pragma config(Motor,  mtr_S1_C3_2,     Winch,         tmotorTetrix, openLoop, reversed)
#pragma config(Servo,  srvo_S1_C4_1,    Hook,                 tServoStandard)
#pragma config(Servo,  srvo_S1_C4_2,    Arm,                  tServoStandard)
#pragma config(Servo,  srvo_S1_C4_3,    servo3,               tServoNone)
#pragma config(Servo,  srvo_S1_C4_4,    servo4,               tServoNone)
#pragma config(Servo,  srvo_S1_C4_5,    servo5,               tServoNone)
#pragma config(Servo,  srvo_S1_C4_6,    servo6,               tServoNone)
//*!!Code automatically generated by 'ROBOTC' configuration wizard               !!*//

// ***********	Globals *********

int deadband = 10;
int mode = 1;

// *********** Include files ********

#include "JoystickDriver.c"	 //Include file to "handle" the Bluetooth messages.
//#include "turn_gyro2.c"  // Include for gyro
#include "Buttonmap.h"

// *********** Prototypes ********
task drive();
//task main ();
task Arm1  ();
//task EndGame();


/////////////////////////////////////////////////////////////////////////////////////////////////////
//
//																		initializeRobot
//
// Prior to the start of tele-op mode, you may want to perform some initialization on your robot
// and the variables within your program.
//
// In most cases, you may not have to add any code to this function and it will remain "empty".
//
/////////////////////////////////////////////////////////////////////////////////////////////////////

void initializeRobot()
{
	servo[Arm] = 200; //Presets arm servo to 110
	//motor[Block_Arm] = 90;
	//wait10Msec(250);
	//motor[Block_Arm] = 0;
	// Place code here to sinitialize servos to starting positions.
	// Sensors are automatically configured and setup by ROBOTC. They may need a brief time to stabilize.
  nMotorPIDSpeedCtrl[Right_Side]= mtrSpeedReg;
	nMotorPIDSpeedCtrl[Left_Side]= mtrSpeedReg;

	nMaxRegulatedSpeed12V = 1000;
	return;
}


/////////////////////////////////////////////////////////////////////////////////////////////////////
//
//																				 Main Task
//
// The following is the main code for the tele-op robot operation. Customize as appropriate for
// your specific robot.
//
// Game controller / joystick information is sent periodically (about every 50 milliseconds) from
// the FMS (Field Management System) to the robot. Most tele-op programs will follow the following
// logic:
//	 1. Loop forever repeating the following actions:
//	 2. Get the latest game controller / joystick settings that have been received from the PC.
//	 3. Perform appropriate actions based on the joystick + buttons settings. This is usually a
//			simple action:
//			*	 Joystick values are usually directly translated into power levels for a motor or
//				 position of a servo.
//			*	 Buttons are usually used to start/stop a motor or cause a servo to move to a specific
//				 position.
//	 4. Repeat the loop.
//
// Your program needs to continuously loop because you need to continuously respond to changes in
// the game controller settings.
//
// At the end of the tele-op period, the FMS will autonmatically abort (stop) execution of the program.
//
/////////////////////////////////////////////////////////////////////////////////////////////////////

/*task Arm1()
{
	int armPower;
	int armPower_raw;
	int limit = 75;
	int cut = 2.5;
	float Gain2 = 0.07;
	float Gain3 = 0.1;

	while (true)
	{
		getJoystickSettings(joystick);

		if (mode == 1)
			{
				cut = 2.5;
			}
			else if (mode == 2)
				{
					cut = 4;
				}
				else
					{
						cut = 2.5;
					}
		armPower_raw = joystick.joy1_y2;

		if (abs(armPower_raw) > deadband)
		{
			armPower = (armPower_raw - sgn(armPower_raw * deadband));

			armPower = ((armPower * Gain2) * (abs(armPower) * Gain3));

			if (armPower > limit)
			{
				armPower = limit;
			}
			else if (armPower < -limit)
			{
				armPower = -limit;
			}
			motor[Block_Arm] = armPower/cut;
		}
		else
		{
			armPower = 0;
			motor[Block_Arm] = armPower;
		}

		if(joy1Btn( BTN_RB ))
		{
			if (ServoValue[Arm] == 0) //If the arm servo is open
			{
				servo[Arm] = 200; //Closes arm servo
			}
			if(ServoValue[Arm] == 200)
			{
				servo[Arm] = 0; //
			}
		}
if(joy1Btn(BTN_RT))
{
	servo[Arm] = 10; //Force opens arm servo
}
	}
}*/
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

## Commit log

2015-08-05 Adding remainder of docs
    [BOM1.xlsx, Phi Alpha 2014-15 Inventory.xlsx, Priorities, Tasks and Notes.xlsx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]
2015-08-05 Adding Omega's notebook
    [BOM.xlsx, Budget Plan.xlsx, Buisness Plan.xlsx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]
2015-08-05 Adding Alpha's notebook docs
    [3D Model Scoring bucket.skp, Bot sketch.skp, Bucket sketch.skp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]
2015-08-05 Adding remaining misc files
    [BOM1.xlsx, Buy List .xlsx, accel.xlsx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]
2015-08-29 Alpha Equipment list
    asdasdass
    [Master_Equipment_List_PhiAlpha452.ods]
2015-08-29 Tetrix Autodesk Inventor Files
    I went through and converted all of the FTC KOP into usable files for
    Autodesk. They still need to be renamed for easy accessibility.
    [Master_Equipment_List_PhiAlpha452.xlsx, SAMANTHA_CASE_BOTTOM_2012.ipt, SAMANTHA_CASE_TOP_2012.ipt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]
2015-08-31 3D Models
    I began the process of renaming the tetrix parts, still have a little
    ways to go. I also made an assembly of a simple squarebot for an
    example, as well as a rolling wheel assembly that both teams can copy
    into their models instaed of assembling four on their own (not fun i
    tried) As for PHI Alpha, i began to model a possible chassis design that
    we will look at on monday.
    [ChassisDes1.0002.iam, ChassisDes1.0005.iam, ChassisDes1.iam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]
2015-09-01 Master Equipment List
    Parts we need to order. Can be used for Bill of material support at a
    later time.
    [Master_Equipment_List_PhiAlpha452.xlsx]
2015-09-01 2014-15 Phi Alpha Engineering Notebook
    [3D Model Scoring bucket.skp, Bot sketch.skp, Bucket sketch.skp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]
2015-09-01 Phi Alpha Parts list to go buy
    [Phi_BudgetBuyList-r1.xlsx]
2015-09-01 AutoCAD Models
    Tim: T and i worked on some more 3D models. We added axles to the
    WheelNGear model and also made a second model that has a chain gear in
    place of the standard.
    [WheelNChainGear.0001.iam, WheelNChainGear.iam, WheelNGear.iam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]
2015-09-03 AutoCAD Models
    I continued work on the Chassis prototype for alpha and also started to
    make a new chassis assembly for the Kraken Chassis
    [ChassisDes1.0005.iam, ChassisDes1.0008.iam, ChassisDes1.iam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]
2015-09-03 AutoCAD Models
    I continued work on the Kraken chassis and also worked some on some
    other designs
    [ChassisDes1.0008.iam, ChassisDes1.0009.iam, ChassisDes1.iam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]
2015-09-08 AutoDesk Models
    Continued work on the two chassis designs for Alpha
    [Andoid Phone.ipt, ChassisDes1.0009.iam, ChassisDes1.0010.iam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]
2015-09-10 Inventor Files
    I continued work on a model of the practice bot in the book.
    [Cross Bar Assembly.iam, MonteCarloM1.1.0002.iam, MonteCarloM1.1.0003.iam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]
2015-09-10 Inventor Files
    Continued work on the model of the practice bot
    [Tower Assembly.iam, tetrix_axle_spacer-big.ipt, tetrix_axle_spacer-small.ipt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]
2015-09-11 Master Equipment List
    Equipment Order List
    [Master_Equipment_List_PhiAlpha452.xlsx]
2015-09-11 Phi_452_Master-Equipment_List
    Re-organized to put similar parts together.
    [Master_Equipment_List_PhiAlpha452.xlsx]
2015-09-11 Models
    Adjustments
    [Kraken-Q.3.0003.iam, Kraken-Q.3.0004.iam, Kraken-Q.3.iam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]
2015-09-14 AutoCAD Models
    Adjustments and design changes on some assemblies
    [KrackenPlate2.0004.ipt, KrackenPlate2.ipt, KrackenPlate2dimensions.ipt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]
2015-09-18 Master plan
    Master plan tasks for PHI Alpha
    [master plan.ods]
2015-09-22 Phi Contact list update
    added Moss and Bachtelle contacts.
    [2015-16-Phi contact list.xlsx]
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2015-09-22 Wheels, tools, retracting wire
    Corrected errors. Added 2 standard wheels, two sets of standard
    allen-Keys, one chain breaker, and a 2ft section of retractable wire (18
    ga).
    [Master_Equipment_List_PhiAlpha452.xlsx]
2015-09-26 UPDATED BOm
    Added: Treads,polycarbonate, velcro, wire, and options for wheels, color
    sensor, and controler.
    [Master_Equipment_List_PhiAlpha452.xlsx]
2015-09-26 Alpha Notebook
    I began to make a newly formatted Meeting log, and did some file
    organization for the alpha notebook folder
    [Master_Equipment_List_PhiAlpha452.ods, Master_Equipment_List_PhiAlpha452.xlsx]
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2015-09-29 Priority list - initial buy
    Still need to deal with major metal pieces and additional sensors.
    [20150928 Master_Equipment_List_PhiAlpha452.xlsx]
2015-09-29 normal updates
    [Master_Equipment_List_PhiAlpha452.xlsx]
2015-10-02 Tank drive Prototype
    [Assembly1TankDrive.iam]
2015-10-02 inventory
    inventory start.
    [Master_Equipment_List_PhiAlpha452- Inventory.xlsx]
2015-10-02 models and meeting log
    [Troysassembly1.iam, troys chassie.iam]
2015-10-06 Equipment list
    YAAAQAAAAAA
    [Master_Equipment_List_PhiAlpha452- Inventory.xlsx]
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2015-10-20 Tank Drive Update
    The tank drive prototypes and spool model
    [Assembly1TankDrive.0036.iam, Assembly1TankDrive.iam, spool model.ipt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]
2015-10-23 Adding user created OpModes
    [v-ger_bulkhead_block_2.stl]
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2015-11-06 Contact list
    [2015-16-Phi contact list.xlsx]
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2015-11-20 improved the ready to go teleop!
    programmed the wench in there and did bug fixes and improvements.
    [TeleOp.java]
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2015-12-08 improvements
    fixed the servo!
    [TeleOp.java]
2015-12-14 3D Modeling
    JarJarBot 2.0
    [Arm Assembly 1.iam, Base Plate dimensions.ipt, Base Plate.ipt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]
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2015-12-26 Alpha equipment order list
    [REVIZED 12-26 Master_Equipment_List_PhiAlpha452.xlsx]
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
